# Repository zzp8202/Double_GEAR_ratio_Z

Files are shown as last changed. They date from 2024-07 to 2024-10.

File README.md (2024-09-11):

# Double_GEAR_ratio_Z

## Description: 
#### Utilizing the characteristics of a movable pulley system, the original Z belt structure's 4:1 gear ratio has been changed to 8:1, amplifying the stepper motor's static torque. This ensures that the gantry can resist gravity even in the event of a power outage. Additionally, using spherical bearings to connect the linear rails and the gantry makes the connection more reliable.

## Objectives：
#### Reject Sagging
##### Enabling the Voron 2.4 Gantry to Defy Gravity

Voron 2.4 uses a belt-driven Z gantry structure. Voron 2.4 theoretically can achieve smaller layer lines compared to most 3D printers that use lead screw structures Due to the linearity of the lead screw affecting the stability of the horizontal position. However, with the original design's 5:1 gear ratio, the static torque of the stepper motor is insufficient to support the heavy gantry in the event of a power outage, especially when mods such as nozzle cleaner and klicky are added to the gantry, further increasing its weight. Since the rear weight of the gantry is significantly greater than the front, the gantry tilt is inevitable, requiring multiple calibrations before each print to achieve an acceptable parallelism with the print bed. To prevent the print head from hitting the platform during leveling, a higher leveling height is also necessary. In my opinion, a bigger issue is that in a power-off state, the gantry and the main frame might stretch, posing unknown deformation risks.

Previously, I modified the original G-code M84 to never turn off the Z motors unless an emergency stop or power cut occurs, to prevent significant gantry tilt.

Additionally, in the current setup, the connection between the gantry and the linear rails is in a 'semi-connected' state, requiring high calibration efforts and even risking disconnection during printing.

In my modification, I used GE5C spherical bearings to connect the gantry and the linear rails, which should provide a more stable structure. I also used a pulley system to increase the gear ratio to 10:1, allowing the gantry to maintain its position without external forces after a power outage. Practical tests show that only one leveling attempt is needed after a power outage without external influences, compared to the previous 3-4 attempts needed to complete the leveling.

## Image:
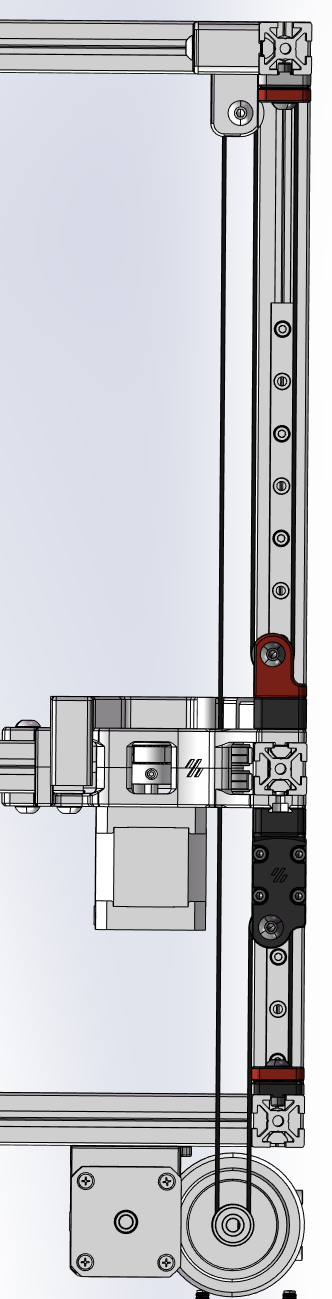
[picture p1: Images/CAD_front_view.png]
front

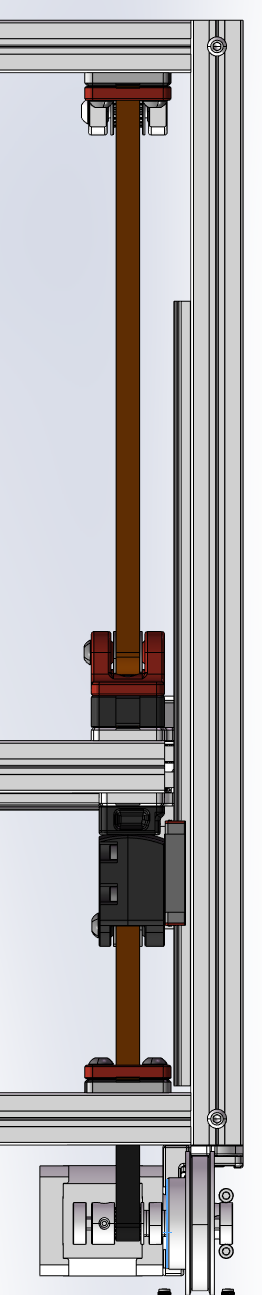
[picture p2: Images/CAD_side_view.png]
side

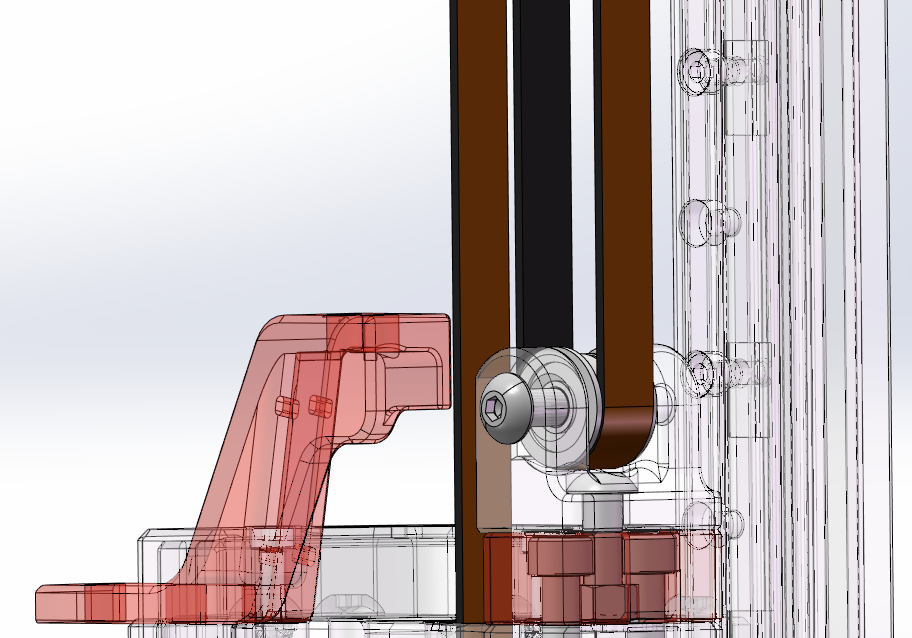
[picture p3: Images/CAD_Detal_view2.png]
Detal2

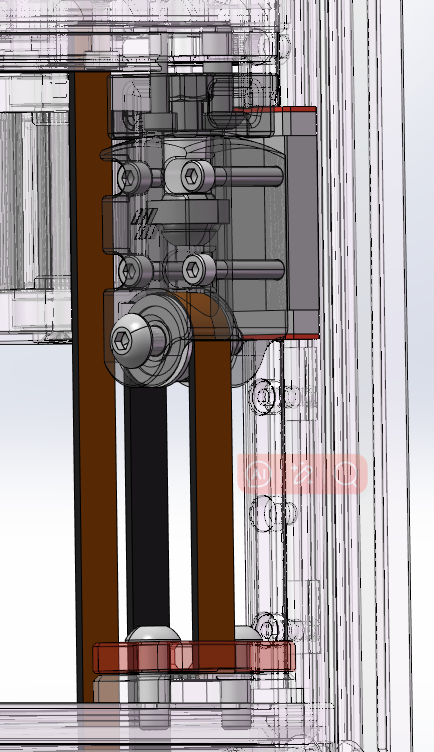
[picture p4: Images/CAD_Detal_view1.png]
Detal1


## Assemble Instructions:
You can replace Z0~Z3 one by one. 

When installing the pulleys, threading the belt in advance will make the process easier.

1. Secure the gantry.you can use this MOD https://mods.vorondesign.com/details/p80KEQX34UKwVvovF0ig
2. Remove the existing Bearing Block and related modules.
3. Loosen the belt tensioning structure.
4. Install the bottom belt clamp.
5. Assemble the Bearing Block Bottom With Pulley module.
6. Assemble the Pulley Holder module.
7. Install the top belt clamp.
8. Restore the belt tensioning structure.
9. Adjust the belt tension.
10. Replace the XY drag chain bracket.

#### Pulley_Holder
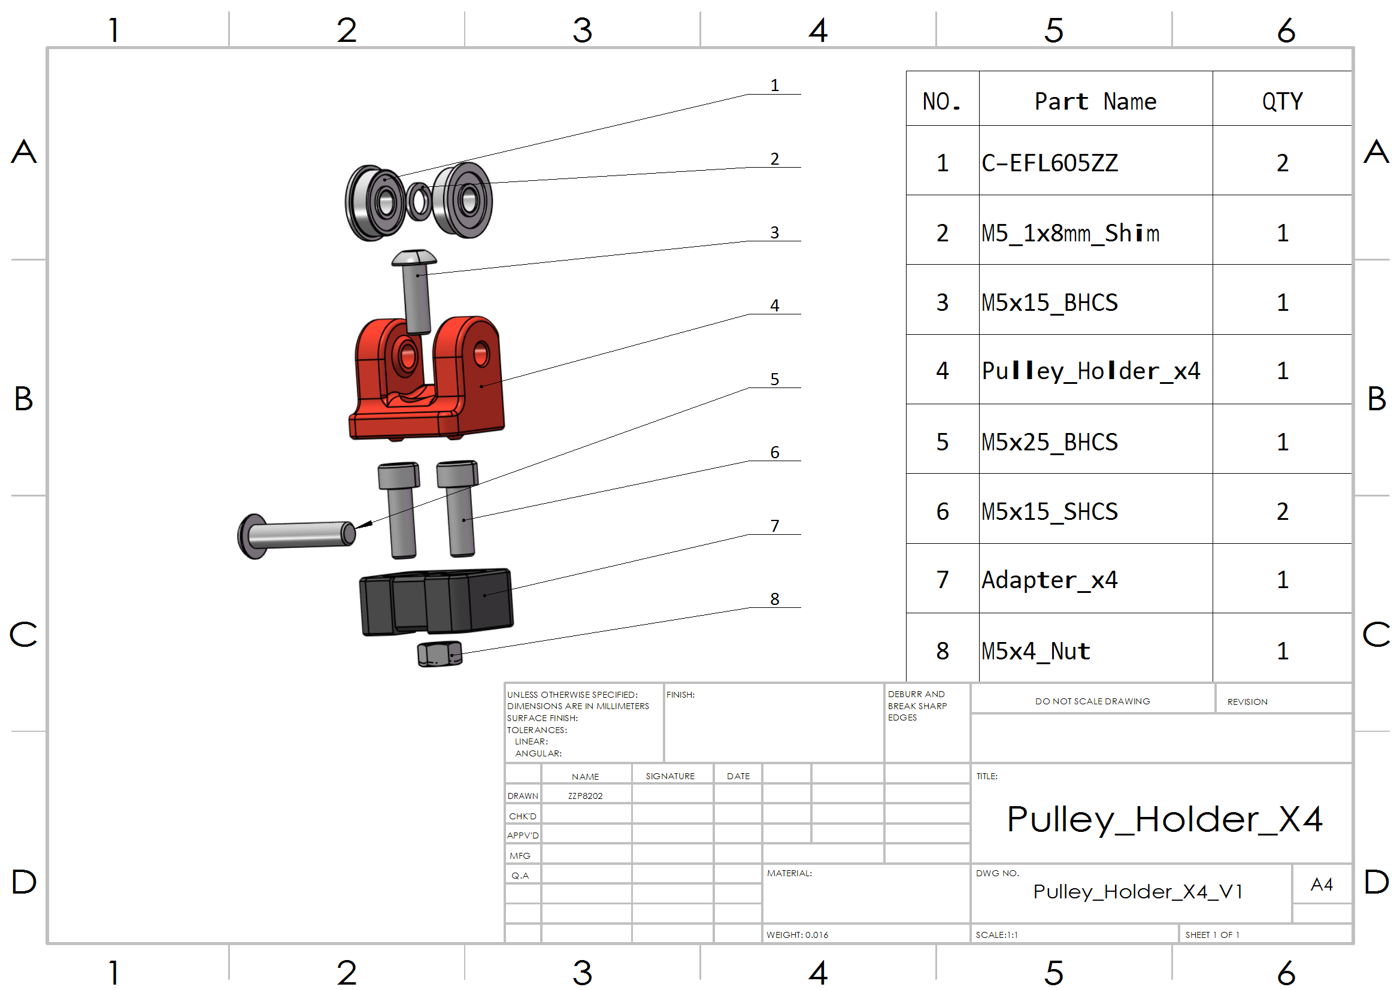
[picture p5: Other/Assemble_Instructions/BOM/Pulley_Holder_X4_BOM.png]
Pulley_Holder_BOM

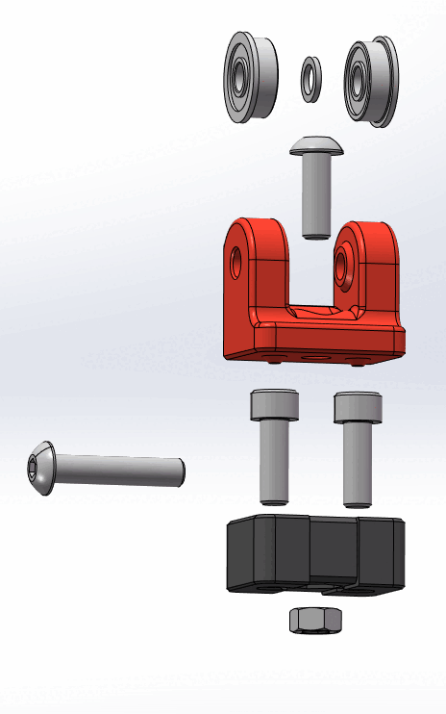
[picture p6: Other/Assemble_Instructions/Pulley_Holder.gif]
Pulley_Holder_Assemble Instructions


#### Bearing_Block_Bottom_With_Pulley
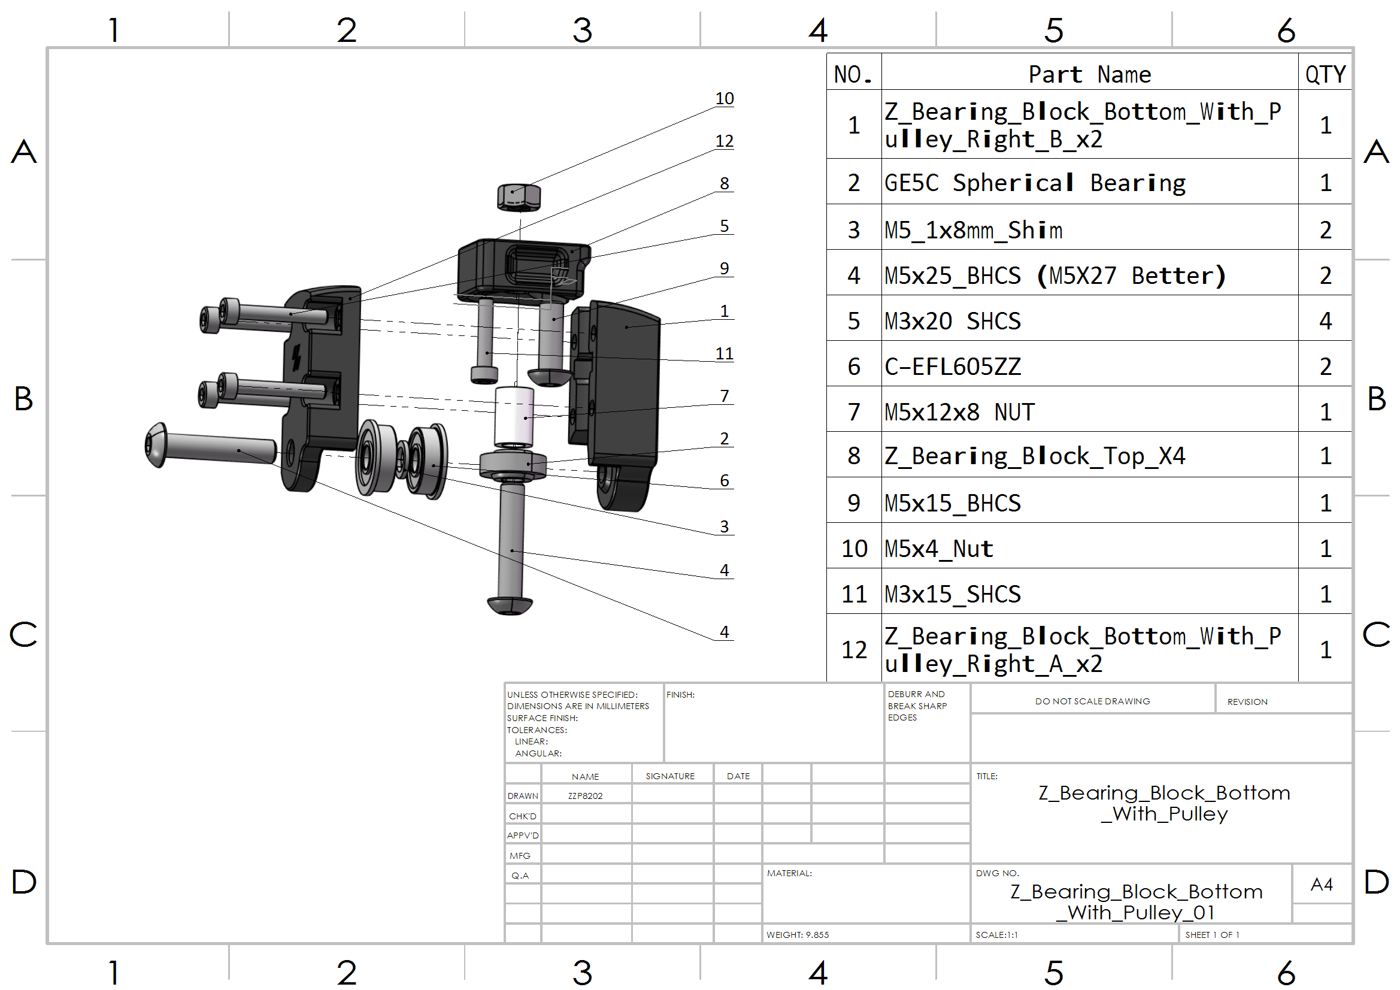
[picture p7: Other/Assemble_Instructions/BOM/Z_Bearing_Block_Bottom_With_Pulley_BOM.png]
Z_Bearing_Block_Bottom_With_Pulley_BOM

Bearing_Block_Bottom_With_Pulley_Assemble Instructions

## Configuration Change:

Find the 'gear_ratio' parameter in 'stepper_z', 'stepper_z1',' stepper_z2', and ' stepper_z3':
Change from 80:16 to 10:1.
I recommend add a gearboxes,like below
```ini
gear_ratio: 80:16, 2:1
```

### Optional Configuration Change:

You may adjust the 'horizontal_move_z' parameter in '[quad_gantry_level] 'and '[bed_mesh]' to reduce the Z-axis lift height during operations, thereby increasing speed. I have change it to '10'.

## Bill of Materials (BOM)：
|NO.	|Category	|Part Name						|Qty				|Remark
|--|--|--|--|--|
|1	|Fasteners	|M3x15 SHCS 							|4				|		|
|2	|Fasteners	|M3x20 SHCS 							|16	 	|	  |
|3	|Fasteners	|M5X25 BHCS 						|12				|M5X27 BHCS Better|
|4	|Fasteners	|M5x15 BHCS 							|24				|		|
|5	|Fasteners	|M5x15 SHCS 							|8				|		|
|6	|Fasteners	|M5xNUT								|8				|		|
|7	|Fasteners	|M5x12x8 NUT 						|4				|LEN:12mm,Out DIA:8mm	|
|8	|Fasteners	|M5X1x8 washer 						|8				|		|
|9	|Fasteners	|M5 T-nut HNTAJ5-5					|16				|		|
|10	|Motion		|F605zz  Bearing 						|16				|		|
|11	|Motion		|GE5C Spherical Bearing 				|4				|		|
|12	|Motion		|GT2 Open Belt LL-2GT-9 (9mm wide)		|Increase 50%		|		|

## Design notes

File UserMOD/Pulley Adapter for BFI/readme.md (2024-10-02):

# Pulley Adapter Mod
This is an adapter modification to allow for anyone using the Beefy Front Idler mod to also use this mod. This replaces the front top Adapter blocks with a block that has one M5 and one M3 hole instead of 2x M5 holes. The Adapter was also shortened to better match the BFI flange that this would sit on top of.

The STL file should contain the two blocks. They are already sized per VORON spec and should be printed in either ABS or ASA. 

Pulley Adapter (BFI) v3

## *Print Settings:*
Voron Spec
Top/Bottom Layers: 5
Walls: 4
Infill: Up to 40%
Infill Pattern: Your choice (I used Cubic)
No supports needed.

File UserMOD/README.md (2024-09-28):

I welcome users to submit mods, but not everyone’s printer is the same as yours, and often I cannot verify your mod.

Therefore, please do not modify the original files. Instead, create a new folder under the 'usermod' directory with your name and place your mod in this folder. Please also provide a brief introduction explaining why users should use your mod.

It's not mandatory, but it would be even better if you could refer the requirements of VORON.

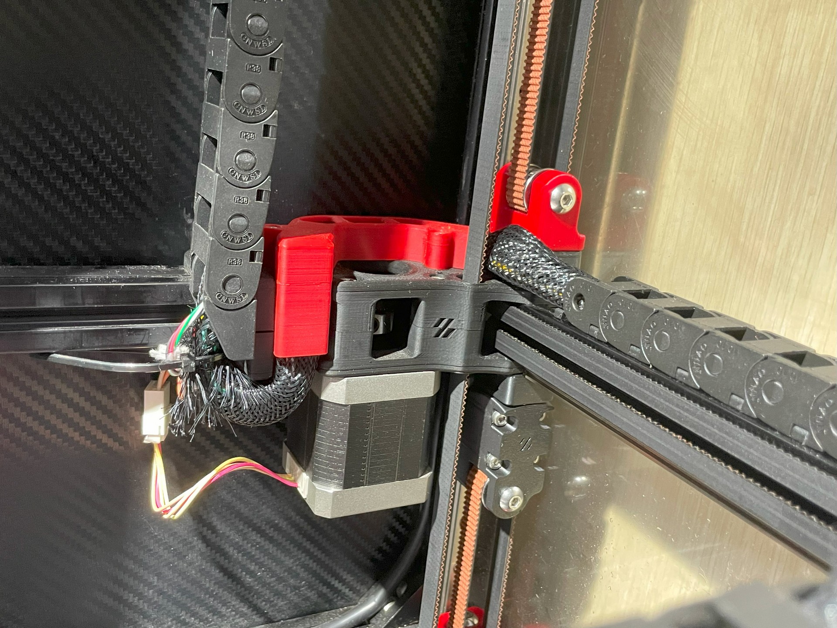
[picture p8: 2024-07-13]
Images/Photo.jpg

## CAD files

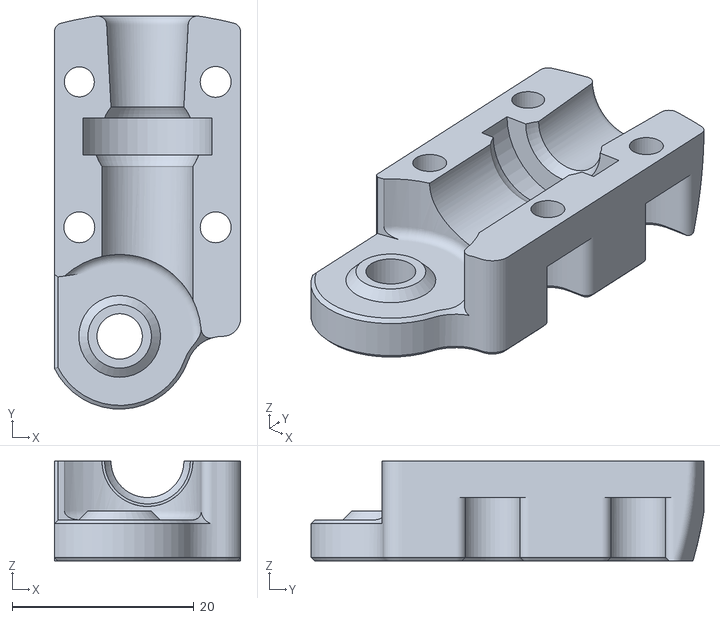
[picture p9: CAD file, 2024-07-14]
STL/Z_Bearing_Block_Bottom_With_Pulley_Left_A_x2.STL
20.5 x 43.2 x 11.0

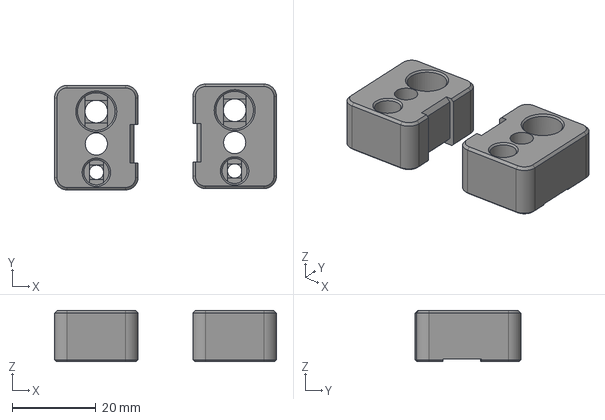
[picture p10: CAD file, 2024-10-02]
UserMOD/Pulley Adapter for BFI/Pulley Adapter (BFI).step
53.1 x 25.3 x 12.2 mm

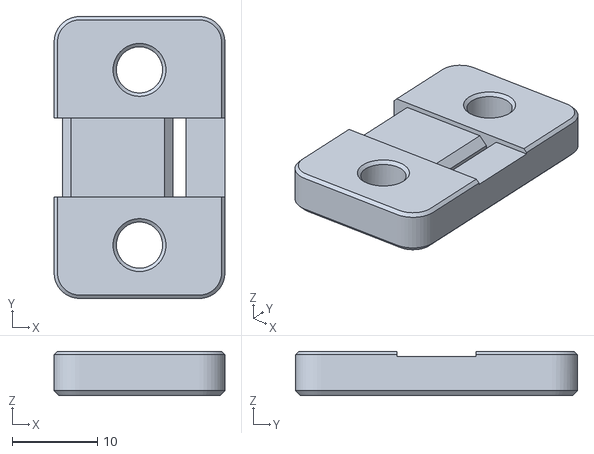
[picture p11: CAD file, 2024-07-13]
STL/Z_Belt_Clamp_Upper_x8.STL
20.0 x 33.0 x 5.20

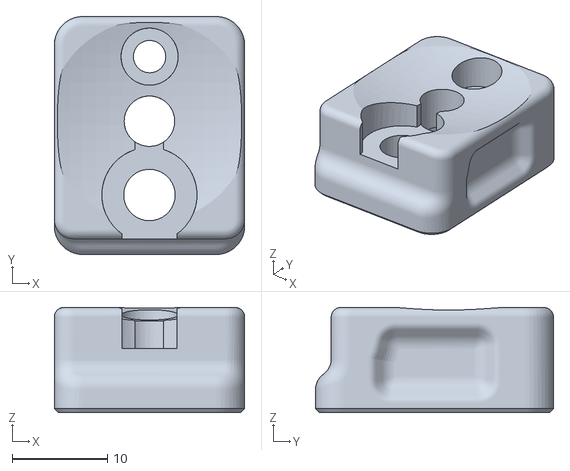
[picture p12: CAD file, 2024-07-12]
STL/Z_Bearing_Block_Top_X4.STL
20.0 x 25.0 x 11.0

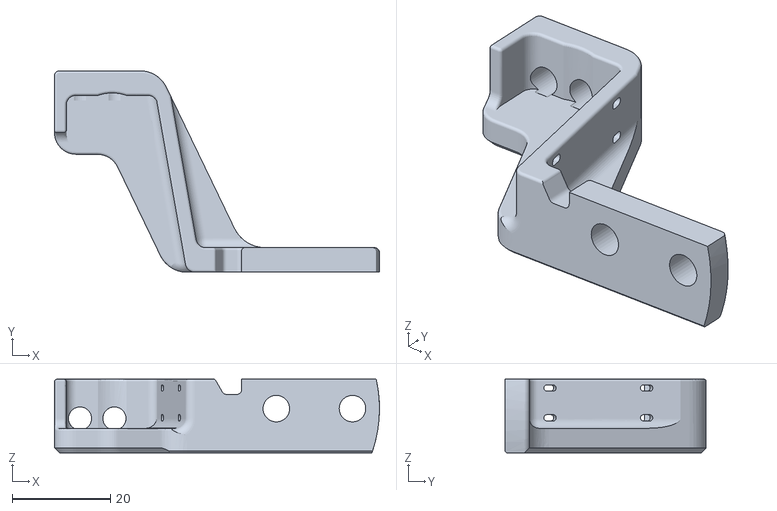
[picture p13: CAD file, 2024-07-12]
STL/XY_Cable_Chain_Brdge_x1.STL
66.1 x 41.0 x 15.0

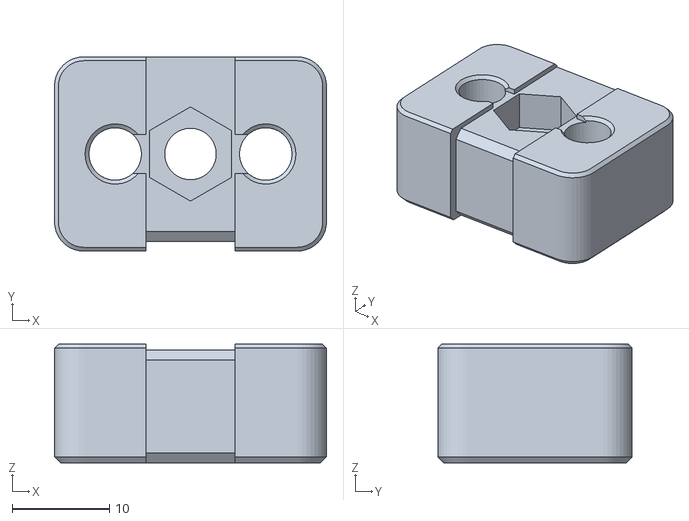
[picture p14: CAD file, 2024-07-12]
STL/Adapter_x4.STL
28.0 x 20.0 x 12.2

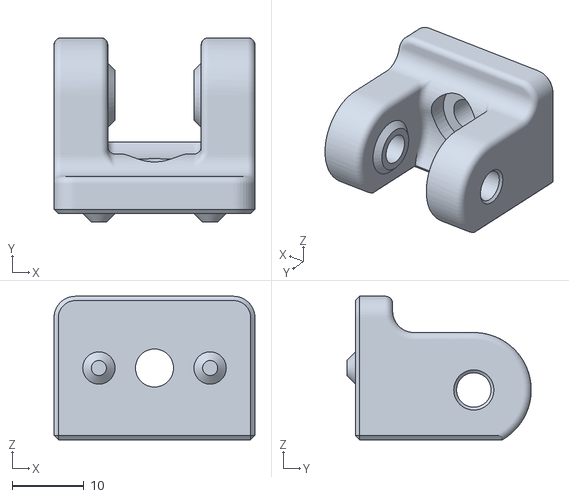
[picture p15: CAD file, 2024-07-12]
STL/Pulley_Holder_x4.STL
28.0 x 25.7 x 20.0

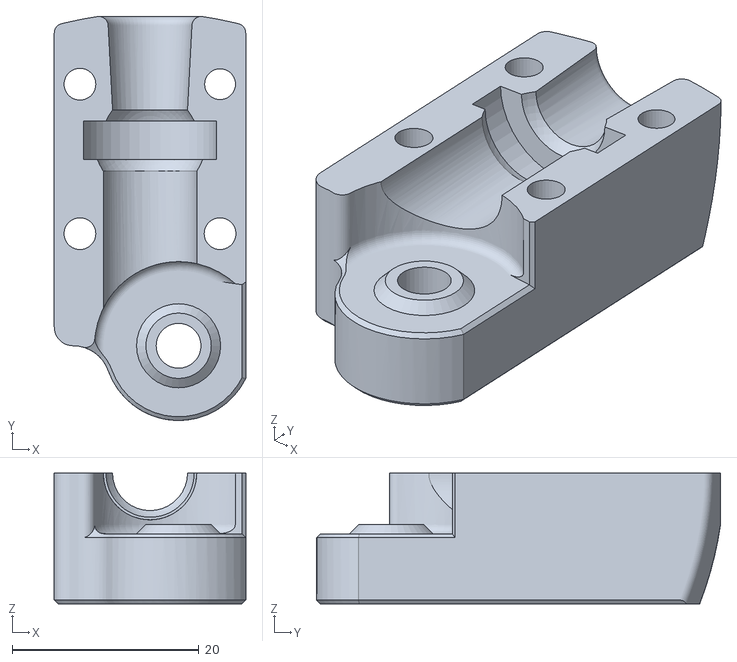
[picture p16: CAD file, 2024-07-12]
STL/Z_Bearing_Block_Bottom_With_Pulley_Left_B_X2.STL
20.5 x 43.2 x 14.0

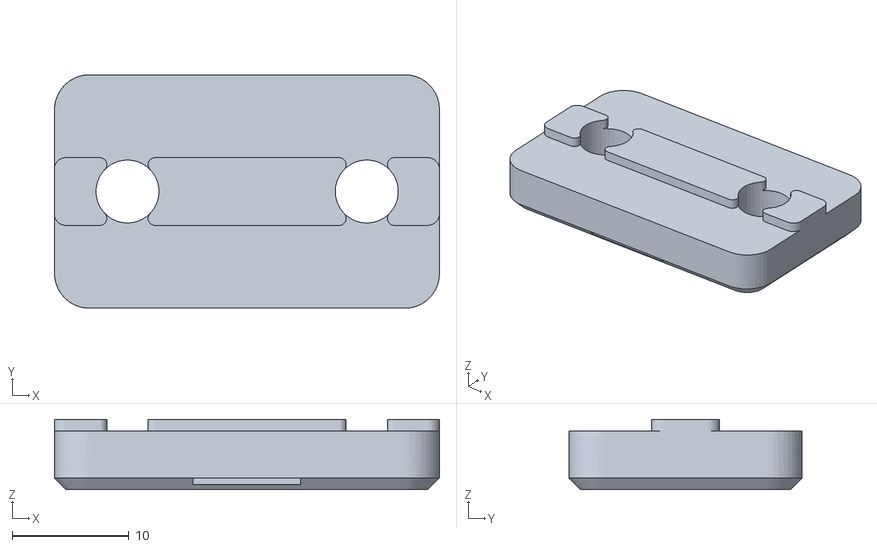
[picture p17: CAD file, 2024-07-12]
STL/Z_Belt_Clamp_Bottom_x8.STL
33.0 x 20.0 x 6.00

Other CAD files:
STL/Z_Bearing_Block_Bottom_With_Pulley_Right_A_x2.STL
STL/Z_Bearing_Block_Bottom_With_Pulley_Right_B_X2.STL
UserMOD/Pulley Adapter for BFI/Pulley Adapter (BFI).stl

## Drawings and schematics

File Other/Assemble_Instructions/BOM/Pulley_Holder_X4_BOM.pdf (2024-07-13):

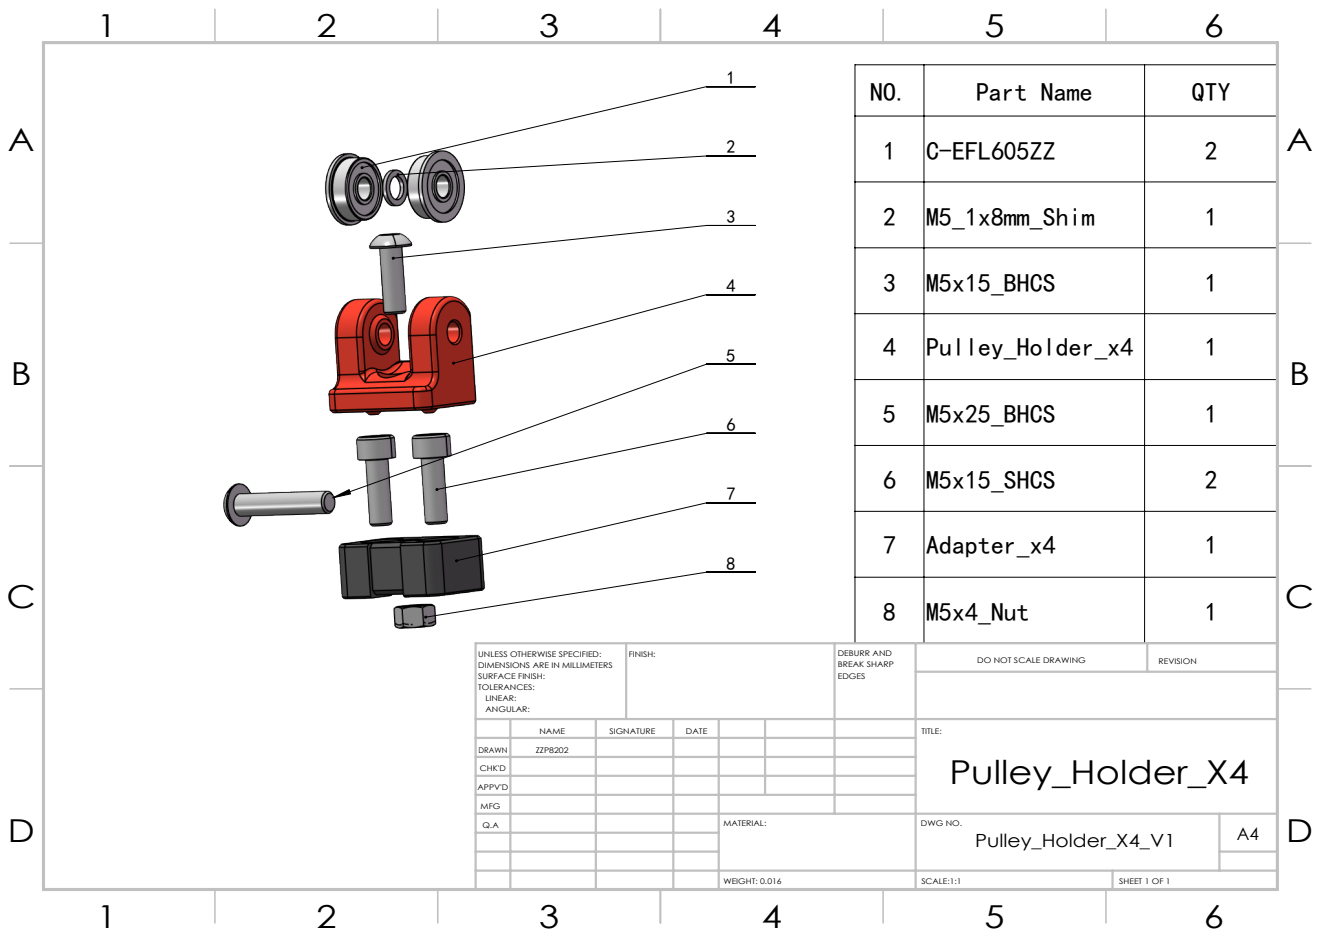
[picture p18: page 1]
SCALE:1:1; SHEET 1 OF 1; WEIGHT: 0.016

NO. | Part Name | QTY

1 | C-EFL605ZZ | 2

2 | M5_1x8mm_Shim | 1

3 | M5x15_BHCS | 1

4 | Pulley_Holder_x4 | 1

5 | M5x25_BHCS | 1

6 | M5x15_SHCS | 2

7 | Adapter_x4 | 1

8 | M5x4_Nut | 1

UNLESS OTHERWISE SPECIFIED: DIMENSIONS ARE IN MILLIMETERS SURFACE FINISH: TOLERANCES: LINEAR: ANGULAR: | FINISH: | DEBURR AND BREAK SHARP EDGES | DO NOT SCALE DRAWING | REVISION

NAME | SIGNATURE | DATE | | | | TITLE: Pulley_Holder_X4

DRAWN | ZZP8202
CHK'D
APPV'D
MFG
Q.A | | | | MATERIAL: | DWG NO. Pulley_Holder_X4_V1 | A4

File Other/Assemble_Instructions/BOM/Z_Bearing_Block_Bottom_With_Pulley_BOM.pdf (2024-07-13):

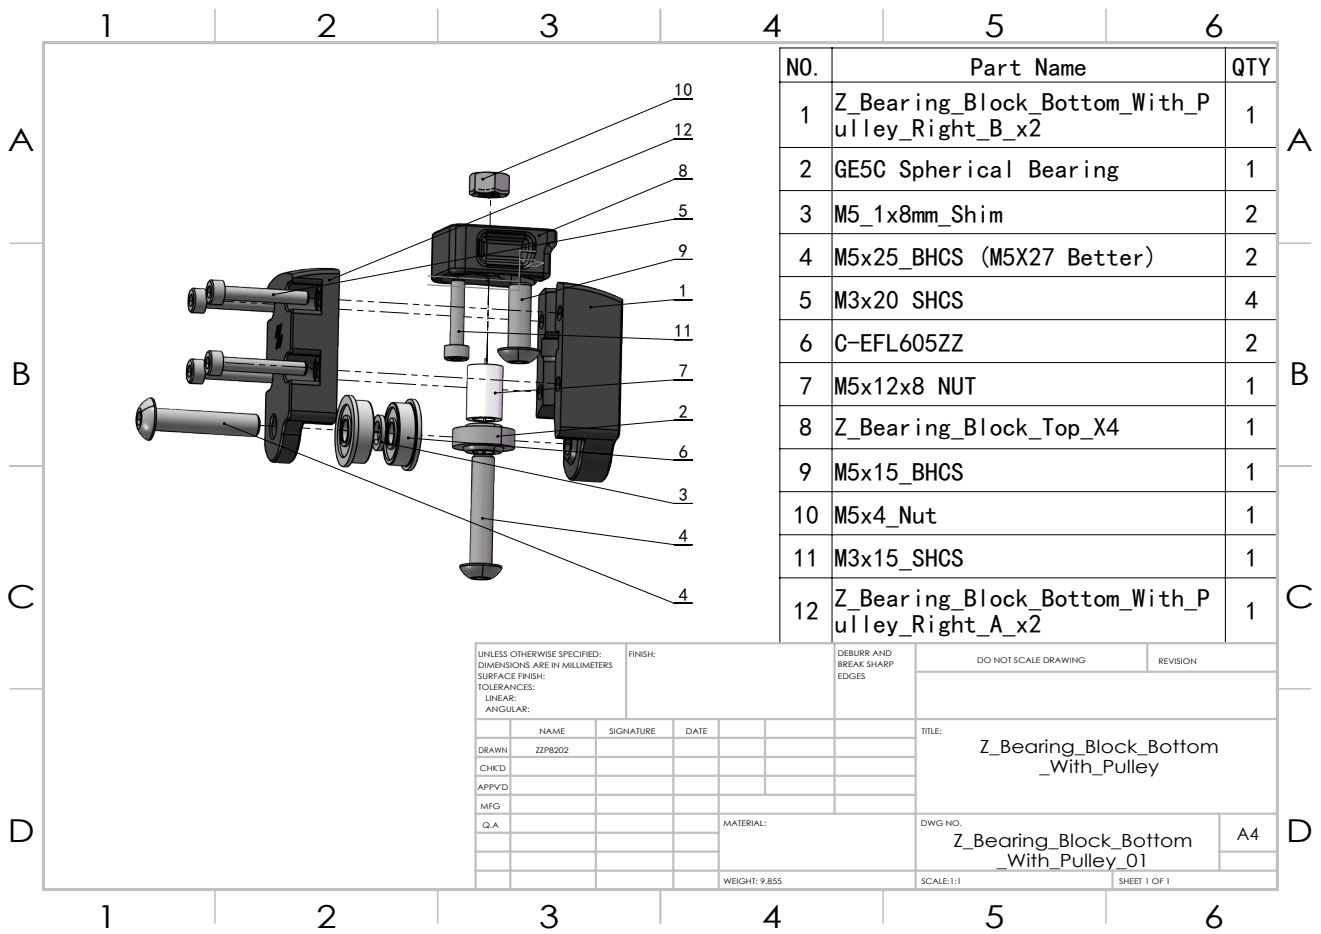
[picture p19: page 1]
SCALE:1:1; SHEET 1 OF 1; WEIGHT: 9.855

NO. | Z_Bearing_Block_Bottom_With_P Part Name | QTY 1
ulley_Right_B_x2 | 1

2 | GE5C Spherical Bearing | 1
3 | M5_1x8mm_Shim | 2
4 | M5x25_BHCS (M5X27 Better) | 2
5 | M3x20 SHCS | 4
6 | C-EFL605ZZ | 2
7 | M5x12x8 NUT | 1
8 | Z_Bearing_Block_Top_X4 | 1
9 | M5x15_BHCS | 1
10 | M5x4_Nut | 1
11 | M3x15_SHCS | 1
12 | Z_Bearing_Block_Bottom_With_P ulley_Right_A_x2 | 1

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

NAME | SIGNATURE | DATE | | | | TITLE: Z_Bearing_Block_Bottom _With_Pulley

DRAWN | ZZP8202
CHK'D
APPV'D
MFG
Q.A | | | | MATERIAL: | DWG NO. Z_Bearing_Block_Bottom _With_Pulley_01 | A4

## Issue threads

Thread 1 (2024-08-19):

Just passing by for a few questions!

Durahl, 2024-08-19:
Greetings!

I just came across your MOD over on the Voron MODs page and was quite intrigued because of my Setup since I'm running _even heavier_ than [Stock LDO-42STH60-3004MAC (S40) Stepper Motors](https://i.imgur.com/NWVWd6k.jpeg) but before considering the change I was wondering about a few things:

- **I don't think it does but just to make sure does this MOD in **_ANY_** kind shift the X / Y location of the Belts?** 🤔
I'm asking because my V2.4 uses a CNCed Deck Panel with low clearance Z-Belt Passthroughs:
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

- **When using a Y-Axis Cable Chain - Doesn't this MOD limit the Gantry's capability of reaching the `Y0` location?**
In my Stock Setup the Bend in the Cable Chain easily touches the Belt at the location where your Upper Gantry Pulley would reside.
Are you using a different `XY Cable Chain Bridge` or different than BOM Spec `Cable Chains`?
Asking because of my Tool Head Filament Cutter Pin being located in the B Drive Idler and in need of reaching `Y3`:
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

- **Reusing the old Belts doesn't seem to be an option as they'll not be having the short, right?** 🤨
( the BOM makes a 50% note which I guess is hinting at this issue? )

Thanks in advance...
Cheers!

Durahl, 2024-08-19:
Ah yea... Found a bit of a Clerance Issue with the Stock Z-Idler Pulley clipping into your Belt attachment Ppoint:
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

zzp8202, 2024-08-19:
Hello Cheers

 Thank you let me know somebody like my mod.

1. It should be compatibility with you CNCed Deck Panel.

2. Also, it compatibility with your Tool Head Filament Cutter Pin.

3. Yes, you should use a new belt to replace the old belt, because we need
a longer belt.

4. Clerance Issue is fixed on STL file.

Durahl ***@***.***> 于2024年8月20日周二 00:06写道：

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

--
。。。。。。。。。。。。。。。。。。。。。。。。。。。。。。。。。
Billy zhang
***@***.***

Closed 2024-09-07.

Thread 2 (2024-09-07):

Found some more issues

Durahl, 2024-09-07:
Greetings again!

I'm about to apply your MOD to my Build and was going over the parts in the CAD once more and noticed a few more issues:
- Pretty much all of the Screws threading into the HEX or T-Nuts suffer from Thread Engagement ( marked in red ).
At least that is the case with common Screw Lengths which I guess is what most ppl will expect 😁
- The Clearance required for the Spacer ( above the GE5C Bearing ) to be able to move at all is insufficient ( marked in purple ).
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
⬇️ Couldn't be bothered to add the T-Nuts into the CAD but I guess one can still see the difference 😁
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

zzp8202, 2024-09-07:
You are right. In many places, I did not take into account the standard bolt length, resulting in insufficient engagement when using standard bolts.

I hope to maximize the Z-space, so I tried to make the structure as compact as possible.
Especially for the structure under the gantry, the overall length must be smaller than the printhead to avoid a situation where the gantry reaches the bottom but the printhead fails to touch the print platform, particularly when the gantry is not leveled.

Regarding the clearance, I want to avoid excessive free travel to control the gantry's tilt in an unlevel state. However, it seems that a little extra margin could be added to reduce stress.

Anyway, it is running well on my machine at the moment, but I also welcome you to submit a PR after verifying your changes, and I will include it as a usermod so that other potential users can see it."

Durahl, 2024-09-08:
Just thought I'd mention it 😁

Based on the below Screengrabs it should be able to deal with the slight increase in Assembly Height - It adds about 2.6mm:
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
I'm using **_heavy_** 60mm Tall Stepper Motors ⬆️ together with an underslung Stepper Motor Fan Mount which I think still leaves about 5mm of Space below it ⬇️
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
In Hindsight though this may be unique to my Build since I'm also using one of those Kinematic Bed Mounts which raise the Bed to ~45mm above the Deck Panel 🤔 I unfortunately also cannot be bothered to create a complete CAD assembly with all of my changes inside for verification 🤣

As for sharing the changes...
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
Besides the change in Geometry to match the sleeker look of my Gantry Parts I'm also using counterbored [Ultra Low-Profile Socket Head Cap Screws](https://i.imgur.com/RDxKGct.jpeg) for most of the M5 Hardware ( Fusion doesn't have them in their Fasteners Library so I'm using placeholder BHCS that are larger in Diameter and thus wouldn't fit ) used in my Designs which makes my parts incompatible for others unless they go out of their way obtaining those 😏

Durahl, 2024-09-11:
Thought I'd be reporting back once more 😉
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

In particular concerning the discussion of a potential Clearance Issue between the Lower Pulley and the Belt Retainer... 🔽
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
...with the Nozzle touching the Bed. **Taking my custom Bed into consideration** - I'd say there being no issues even with stock Bed Mountings and perhaps a thinner Bed as there's plenty of space left between the Parts to enable more thread Engagement.

Btw... While trying to figure out how the Ratio would have to be setup I came across your Instruction of changing it from 4:1 to 8:1 which kinda got me stumped for a moment since the default Ratio for a V2.4 is 80:16... I assume you're running a 20T Pulley against an 80T one instead of the recommended 16T against an 80T? 🤔

Perhaps consider rewriting the Instructions to inform ppl to double the Higher of the two Numbers - So turning `4`:1 ➡️ `8`:1 or `80`:16 ➡️ `160`:16

Anyways... Thanks for the MOD! 😁

zzp8202, 2024-09-11:
Thank you for your feedback.

About the distance between the Lower Pulley and the Belt Retainer, it should have enough space to enable more thread Engagement, because the gantry will not incline any more. but I will not improve it in the short term because I am so lazy and it can be work. :P
BTW: I am not a professional CAD owner, it took me a lot of time.

For the parameter 'gear_ratio', I made a mistake, I will recommend add a gearbox, like below.
'gear_ratio: 80:16, 2:1'

Closed 2024-09-28.

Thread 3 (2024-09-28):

BFI Integration

sphyx42, 2024-09-28:
Hello There!!

I'm working on integrating your mod into my build and noticed that the front top pulley adapter is sized for the original Front Idler setup with 2x M5 bolts. Since I'm running the BFI mod, the Pulley Adapter doesn't work out.

I was unable to add a pull request for some reason, probably because I'm newer at doing that stuff in Github; but I adapted the adapter to fit the BFI: I shortened it by 3mm and replaced one M5 bolt hole for an M3 bolt hole and ensured everything lined up on the BFI.

I can share both the CAD and STL with you, just not sure how at the moment.

Thanks!!

zzp8202, 2024-09-28:
I saw your Pull requests, please see the comment in pull requests.

Closed 2024-09-28.

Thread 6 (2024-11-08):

Belt clamps rub against upper idlers

BladeRunner28, 2024-11-08:
I have printed and installed this mod on my Voron 2.4r2 and have noticed that the upper geared idlers rub against, and cut into, the upper belt clamps.

I doubt this is by design, is there a modification of the belt clamps that account for the upper idlers so that they don't interfere?

zzp8202, 2024-11-08:
Clerance Issue between idlers and belt clamps should be fixed on STL file，（3Dfile still with this issue. ）
If you use the STL file to print the belt clamps this problem should not occur. please let me know what model number of idler you use.
BTW: If you can take a photo will let me know clearly.

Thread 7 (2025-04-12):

Belt length

Bata3, 2025-04-12:
Can you please tell me how many mm are needed for one Z axis of the GT belt? I have a voron 2.4 300, if I understand correctly, it is about 1700 mm?
Is the belt tensioning done as standard, like on a Voron?
thank you

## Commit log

2024-07-13 Add Assemble_Instructions
    [Pulley_Holder_X4.SLDDRW, Z_Bearing_Block_Bottom_With_Pulley.SLDDRW]
2024-07-13 upload gif
    [Pulley_Holder_X4.SLDDRW, Z_Bearing_Block_Bottom_With_Pulley.SLDDRW]
2024-07-14 FIX Voron logo
    [Z_Bearing_Block_Bottom_With_Pulley_Left_A_x2.STL, Z_Bearing_Block_Bottom_With_Pulley_Right_A_x2.STL]
2024-09-28 Add files via upload
    Modified Pulley Adapter to accommodate BFI Screw setup.
    [Pulley Adapter (BFI) v2.step, Pulley Adapter (BFI) v2.stl]
